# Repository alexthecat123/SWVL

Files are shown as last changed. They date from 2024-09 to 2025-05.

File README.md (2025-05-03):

# SWVL: An AI-powered face tracking camera gimbal.

This GitHub repo contains all of the files for the SWVL gimbal hardware and software. SWVL was created by me (Alex Anderson-McLeod), Kuba Jerzmanowski, Jagger Tanner, Trevor Allison, and Michael Laitarovsky as our senior Capstone project at the University of South Carolina.

Most of the files in the root directory were for testing purposes and can be ignored. All of the SWVL software for the host computer, including the Electron frontend and Python backend, are in the sw directory, and everything hardware-related (the CAD files for the gimbal itself, the control PCB design, and the code running on the control board) can be found in the hw directory.

The one file in the root directory that might actually be useful to you is SWVL_Paper.pdf. This paper describes the entire project in great detail, covering our objectives, methodology, and results.

We were unable to upload the model itself to GitHub because of its large size, so you can find it [here](https://emailsc-my.sharepoint.com/:f:/g/personal/aja4_email_sc_edu/ErGuz_QFEuFKh9op3Ph_HMUBoIsI0FKV3FtuGb-c4GJ2zg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) instead. For some stupid reason, USC has disabled the "anyone with the link can view" option when sharing files in OneDrive, so this link will only work for other people from the university. I have no idea why they would do this, but if you're outisde the university and want access, send me an email and I'll get you the files. The latest one is best_dev_loss0476_dsc.pth, but there are also older versions in that directory if you're interested in the improvements we made throughout the development process.

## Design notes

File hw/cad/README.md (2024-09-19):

# SWVL CAD Files

This directory contains all of the CAD files for the SWVL gimbal, which will be 3D-printed to form the final gimbal structure.

## Endstop Pins
- Quantity: 4
- Supports: No
- Infill: 100%
- Layer Height: 0.1mm-0.2mm

## Pan Axis
- Quantity: 1
- Supports: Yes
- Infill: 20%
- Layer Height: 0.1mm-0.2mm

## Everything Else
- Quantity: 1
- Supports: No
- Infill: 20%
- Layer Height: 0.1mm-0.2mm

## Other Parts
One of [these bearings](https://www.amazon.com/dp/B082PRVZ7B) should be inserted into the hole in the bearing riser, and four of [these screws](https://www.amazon.com/dp/B01B1OD4Y2) should be used to secure the motor to the motor riser.

## Todo
ADD AN ASSEMBLY DRAWING TO SHOW HOW EVERYTHING GOES TOGETHER!

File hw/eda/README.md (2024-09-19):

# SWVL EDA Files

This directory contains all of the EDA files for the SWVL gimbal hardware, including PCB Gerbers and schematics.

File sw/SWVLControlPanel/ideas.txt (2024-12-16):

It's stupid, but the way the camera thing will have to work is to make a virtual camera with pyvirtualcam that can be forwarded to Electron. But this requires OBS on Mac/Win, and a special package on Linux, which the Electron app will need to auto-install for us in its final version.
Camera and serial port are separate. Should camera autoconnect, but serial not autoconnect?

Maybe have one screen where it asks you to connect to the gimbal, and then only proceed to the main control panel once you're connected.

How should Python pick which camera to use? Should Electron tell it?

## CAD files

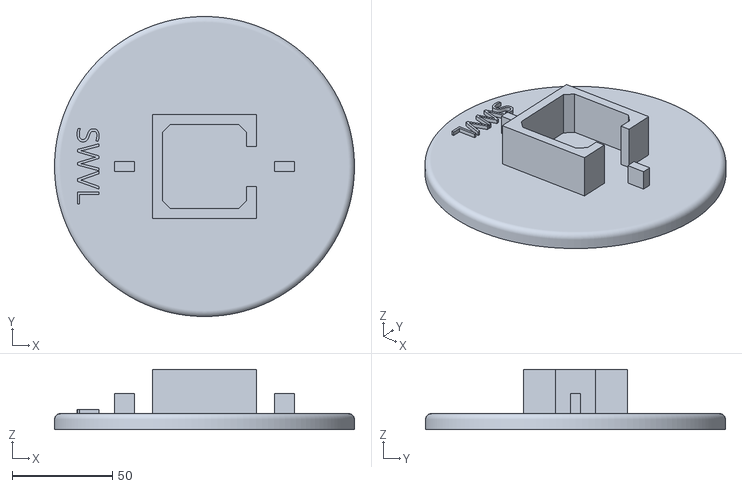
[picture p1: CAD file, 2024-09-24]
hw/cad/SWVL Gimbal Base.stl
150.0 x 150.0 x 30.0

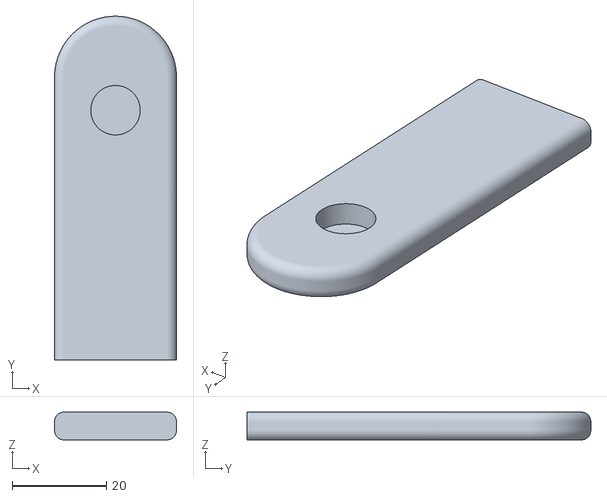
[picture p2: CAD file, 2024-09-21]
hw/cad/SWVL Gimbal Riser - Bearing Side.stl
25.9 x 72.9 x 5.90

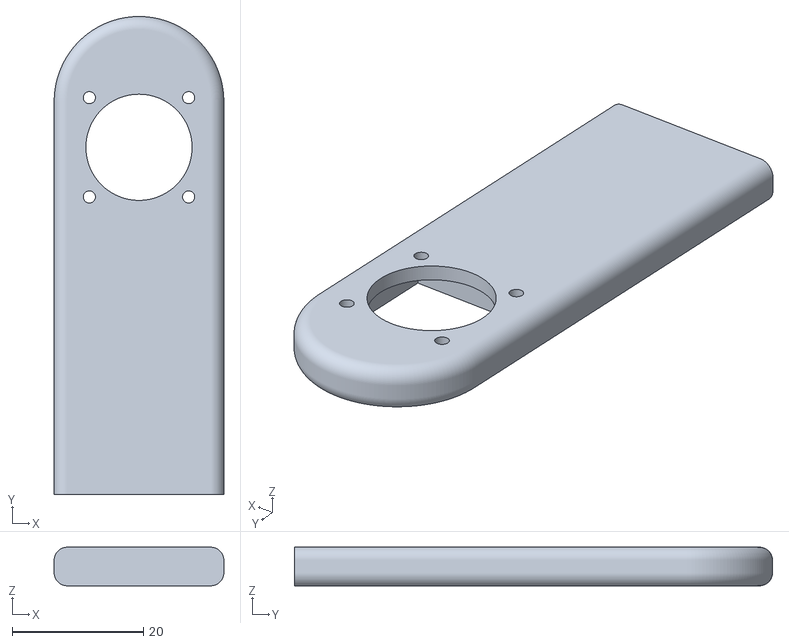
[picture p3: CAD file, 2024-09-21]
hw/cad/SWVL Gimbal Riser - Motor Side.stl
25.9 x 72.9 x 5.90

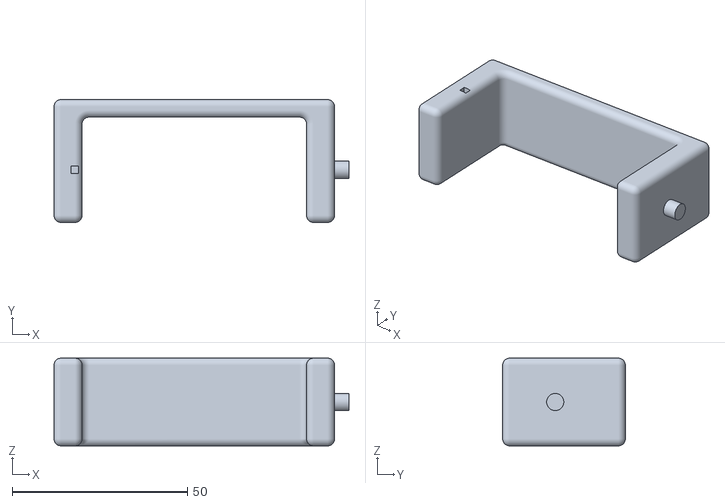
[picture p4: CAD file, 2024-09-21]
hw/cad/SWVL Gimbal Tilt Axis - Generic.stl
84.1 x 35.0 x 25.0

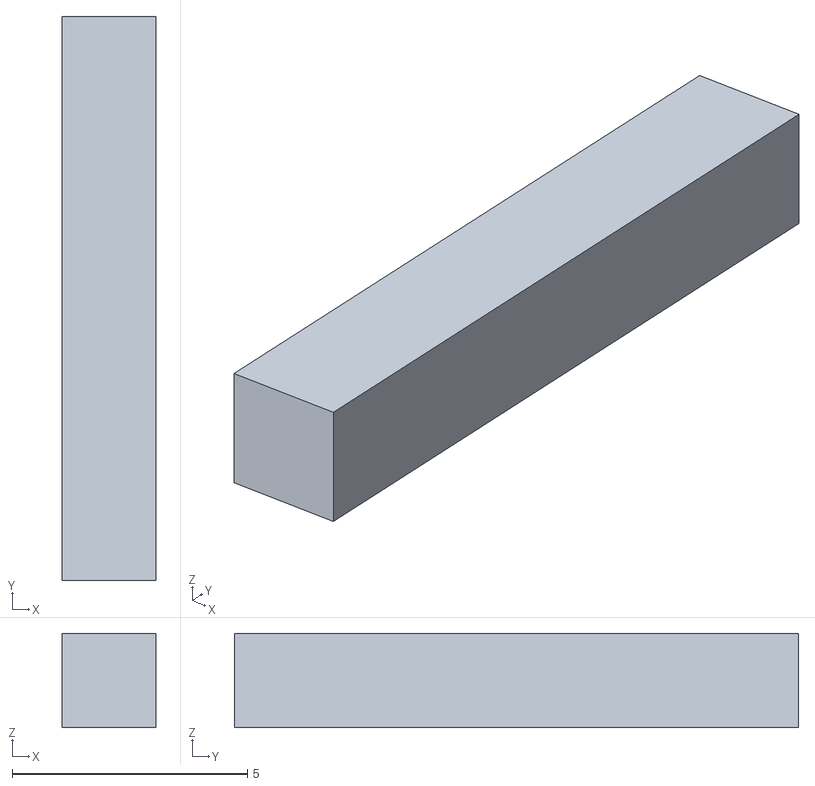
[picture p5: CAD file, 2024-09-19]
hw/cad/SWVL Gimbal Endstop Pin.stl
2.00 x 12.0 x 2.00

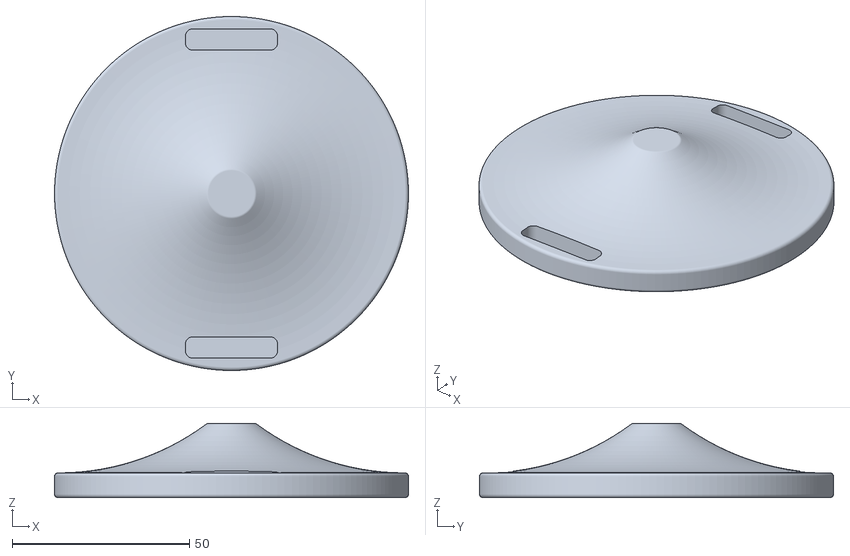
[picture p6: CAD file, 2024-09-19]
hw/cad/SWVL Gimbal Pan Axis.stl
100.0 x 100.0 x 21.0

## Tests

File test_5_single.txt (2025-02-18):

/Users/kuba/Documents/data/Raw/Face-Detection-Dataset/images/val/0a1f6ed36f1bd8bf.jpg
/Users/kuba/Documents/data/Raw/Face-Detection-Dataset/images/val/0a9ae8f9bf2f8b5c.jpg
/Users/kuba/Documents/data/Raw/Face-Detection-Dataset/images/val/0bb621ebf775cb91.jpg
/Users/kuba/Documents/data/Raw/Face-Detection-Dataset/images/val/0be6b78bb96d4c49.jpg
/Users/kuba/Documents/data/Raw/Face-Detection-Dataset/images/val/0be97b86c8baf73f.jpg

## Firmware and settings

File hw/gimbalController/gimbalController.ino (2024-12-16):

// Command HA: Home all axes.
// Command HP: Home pan axis.
// Command HT: Home tilt axis.
// Command PR: Pan relative. Provide 16-bit signed int afterwards representing number of steps.
// Command TR: Tilt relative. Provide 16-bit signed int afterwards representing number of steps.
// Command GP: Get pan angle. Returns 16-bit angle.
// Command GT: Get tilt angle. Returns 16-bit angle.
// Command PS: Play Sandstorm.
// Command SS: Stop playing Sandstorm.
// Command DS: Disable steppers so that the gimbal won't just stay on when the application exits.
// Command ID: Identify command so that control program can ensure that serial device is a gimbal. Returns 8-bit ID byte.

// make homing commands block so that host knows when gimbal has homed

const uint8_t panStep = 2; 
const uint8_t tiltStep = 3;
const uint8_t panDir = 5;
const uint8_t tiltDir = 6;
const uint8_t enable = 8;

int panAngle = 0;
int tiltAngle = 0;

void setup(){
    Serial.begin(115200);
    pinMode(panStep, OUTPUT);
    pinMode(tiltStep, OUTPUT);
    pinMode(panDir, OUTPUT);
    pinMode(tiltDir, OUTPUT);
    pinMode(enable, OUTPUT);
    digitalWrite(panStep, LOW);
    digitalWrite(tiltStep, LOW);
    digitalWrite(panDir, LOW);
    digitalWrite(tiltDir, LOW);
    digitalWrite(enable, HIGH);
}

void loop(){
    getCommand();
}

void getCommand(){
    char commandLetter;
    int commandParam;
    if(Serial.available()){
        delay(1);
        commandLetter = Serial.read();
        delay(1);
        switch(commandLetter){
            case 'H': // Home
                commandLetter = Serial.read();
                if(commandLetter == 'A'){ // All
                    homePan();
                    homeTilt();
                }
                else if(commandLetter == 'P'){ // Pan
                    homePan();
                }
                else if(commandLetter == 'T'){ // Tilt
                    homeTilt();
                }
                else{
                  flushSerial();  
                }
                break;
            case 'P': // Pan or Play
                commandLetter = Serial.read();
                if(commandLetter == 'R'){ // Pan Relative
                    commandParam = Serial.read() << 8;
                    commandParam |= Serial.read();
                    //commandParam = Serial.read();
                    panRelative(commandParam);
                }
                else if(commandLetter == 'S'){ // Play Sandstorm
                    sandstorm(true);
                }
                else{
                  flushSerial();  
                }
                break;
            case 'T': // Tilt
                commandLetter = Serial.read();
                if(commandLetter == 'R'){ // Relative
                    //commandParam = Serial.read();
                    commandParam = Serial.read() << 8;
                    commandParam |= Serial.read();
                    tiltRelative(commandParam);
                }
                else{
                    flushSerial();
                }
                break;
            case 'G': // Get Angle
                commandLetter = Serial.read();
                if(commandLetter == 'P'){ // Pan Angle
                    getPanAngle();
                }
                else if(commandLetter == 'T'){ // Tilt Angle
                    getTiltAngle();
                }
                else{
                  flushSerial();  
                }
                break;
            case 'S': // Stop Sandstorm
                commandLetter = Serial.read();
                if(commandLetter == 'S'){ // Stop Sandstorm
                    sandstorm(false);
                }
                else{
                    flushSerial();
                }
                break;
            case 'D': // Disable Steppers
                commandLetter = Serial.read();
                if(commandLetter == 'S'){ // Disable Steppers
                    digitalWrite(enable, HIGH);
                }
                else{
                    flushSerial();
                }
                break;
            case 'I': // ID
                commandLetter = Serial.read();
                if(commandLetter == 'D'){ // ID
                    delay(1);
                    Serial.println(69);
                    delay(1);
                }
                else{
                    flushSerial();
                }
                break;
            default:
                flushSerial();  
        }
    }
}

void flushSerial(){
    while(Serial.available()){
        Serial.read();
        //delay(50);
    }
}

void homePan(){
    panAngle = 0;
}

void homeTilt(){
    tiltAngle = 0;
}

void panRelative(int commandParam){
    digitalWrite(enable, LOW);
    if(commandParam < 0){
        digitalWrite(panDir, 0);
    }
    else{
        digitalWrite(panDir, 1);
    }
    for(int i = 0; i < abs(commandParam); i++){
        if(commandParam < 0){
            panAngle -= 1;
        }
        else{
            panAngle += 1;
        }
        digitalWrite(panStep, HIGH);
        delay(1);
        digitalWrite(panStep, LOW);
        delay(1);
    }
}

void tiltRelative(int commandParam){
    digitalWrite(enable, LOW);
    if(commandParam < 0){
        digitalWrite(tiltDir, 0);
    }
    else{
        digitalWrite(tiltDir, 1);
    }
    for(int i = 0; i < abs(commandParam); i++){
        if(commandParam < 0){
            tiltAngle -= 1;
        }
        else{
            tiltAngle += 1;
        }
        digitalWrite(tiltStep, HIGH);
        delay(1);
        digitalWrite(tiltStep, LOW);
        delay(1);
    }
}

void getPanAngle(){
    //Serial.print(panAngle >> 8);
    //Serial.print(panAngle);
    Serial.print(panAngle);
}

void getTiltAngle(){
    //Serial.write(tiltAngle >> 8);
    //Serial.write(tiltAngle);
    Serial.print(tiltAngle);
}

void sandstorm(bool state){

}

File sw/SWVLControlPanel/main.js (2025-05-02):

const { app, BrowserWindow } = require('electron')
const { spawn } = require('child_process');
const path = require('path');
const executablePath = path.resolve(__dirname, 'main');
const { exec } = require('child_process');
const os = require('os');
//execCommand('. ../SWVL_venv/bin/activate && python3 python/main.py');
//execCommand('.', ['../SWVL_venv/bin/activate']);
execCommand('../SWVL_venv/bin/python3', ['python/main.py']);
//const child = spawn(executablePath); // UNCOMMENT THIS TO SPAWN THE PYTHON PROCESS AGAIN
const { ipcMain } = require('electron');


const { SerialPort } = require('serialport');
const { kill } = require('process');

const createWindow = () => {
    const win = new BrowserWindow({
        width: 800,
        height: 650,
        webPreferences: {
            preload: path.join(__dirname, 'preload.js'), // Specify the preload script
            contextIsolation: true, // Keep context isolation enabled
            nodeIntegration: false // Disable Node.js integration for security
        }
    })
    win.setMaximizable(false)
    win.setResizable(false)
    win.loadFile('index.html')
  }

setTimeout(() => {
    app.whenReady().then(() => {
        createWindow();
        app.on('activate', () => {
            if (BrowserWindow.getAllWindows().length === 0) createWindow()
        })
    })
}, 1000);

ipcMain.handle('get-serials', async (event, arg1, arg2) => {
    let validPorts = [];
    await SerialPort.list().then((ports, err) => {
        if(err) {
          console.log(err.message);
          return
        }
        //console.log('ports', ports);
        for(let i = 0; i < ports.length; i++){
          if(ports[i].manufacturer != null){
              validPorts.push(ports[i]);
          }
        }
        if(arg1 == true){
            console.log('validPorts', validPorts);
        }
        if (ports.length === 0) {
          console.log('No ports discovered');
        }
    })
    return validPorts; // This will be sent back to the renderer
});

app.on('window-all-closed', (event) => {
    event.preventDefault();
    fetch(`http://127.0.0.1:5000/stop-tracking`,
        {
            method: "GET",
            headers: {
                Accept: "application/json",
                "Content-Type": "application/json",
            },
        }
    ).then(res => res.json()).then((data) => {
        console.log(data);

    })
    setTimeout(function(){
        //child.kill(); // UNCOMMENT THIS TO KILL THE PYTHON PROCESS
        killProcessByName('python3').then(() => {
            console.log('python3 process killed successfully');
        }
        ).catch((error) => {
            console.error('Error killing python3 process:', error);
        });
        killProcessByName('pt_main_thread').then(() => {
            console.log('pt_main_thread process killed successfully');
        }
        ).catch((error) => {
            console.error('Error killing pt_main_thread process:', error);
        });
    },1000);
    setTimeout(function(){
        if (process.platform !== 'darwin') app.quit()
    },1000);
})


function killProcessByName(processName) {
  return new Promise((resolve, reject) => {
    const platform = os.platform();

    let command;

    if (platform === 'win32') {
      command = `taskkill /IM ${processName} /F`;
    } else if (platform === 'linux' || platform === 'darwin') {
      command = `pkill -f ${processName}`;
    } else {
      return reject(new Error(`Unsupported platform: ${platform}`));
    }

    exec(command, (error, stdout, stderr) => {
      if (error) {
        return reject(new Error(`Failed to kill process: ${stderr || error.message}`));
      }
      return resolve();
    });
  });
}

/*function execCommand(command) {
    const child = exec(command);
  
    child.stdout.pipe(process.stdout);
    child.stderr.pipe(process.stderr);
  
    child.on('exit', (code, signal) => {
      console.log(`Command exited with code ${code} and signal ${signal}`);
    });
  }*/

function execCommand(command, args = []) {
    const child = spawn(command, args, { stdio: 'inherit' });
    
    child.on('error', (err) => {
        console.error(`Failed to start command: ${err}`);
    });
    
    child.on('exit', (code, signal) => {
        console.log(`Command exited with code ${code} and signal ${signal}`);
    });
    }


/*child.stdout.on('data', (data) => {   // UNCOMMENT THIS TO SEE THE OUTPUT OF THE PYTHON PROCESS
    console.log(data.toString("utf-8"));
});

child.stderr.on('data', (data) => {
    console.log(data.toString("utf-8"));
});

child.on('error', (error) => {
    console.log(error.toString("utf-8"));
});*/

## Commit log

2024-09-19 initial version of CAD design
    [SWVL Gimbal Base.stl, SWVL Gimbal Endstop Pin.stl, SWVL Gimbal Pan Axis.stl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]
2024-09-19 added printing instructions and mechanical parts info
2024-09-21 tightened tilt axis hole for better shaft fit
    [SWVL Gimbal Tilt Axis - Generic.stl]
2024-09-21 enlarged risers for better fit into pan axis
    [SWVL Gimbal Riser - Bearing Side.stl, SWVL Gimbal Riser - Motor Side.stl]
2024-09-24 hopefully guessed the right stepper chamfer angle this time
    [SWVL Gimbal Base.stl]
2024-12-13 modified gimbalController to disable steppers when control turned off, added tracking thread to Python, implemented commands between Electron/Python, and got the Enable Tracking toggle working
2024-12-14 made sure steppers turn off on app exit
2025-04-29 Adding model and connection to camera with opencv
